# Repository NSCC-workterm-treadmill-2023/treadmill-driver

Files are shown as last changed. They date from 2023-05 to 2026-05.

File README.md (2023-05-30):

# Treadmill Driver

This code is designed to replace the front panel of the Vision Fitness
[T9800 treadmill](https://www.toughtrain.com/vision-fitness/vision-fitness-treadmills/vision-t9800hrt-platform-treadmill) (now discontinued),
interfacing directly with the motor controller board in the bottom.

## Usage

See the [API doc](docs/API.md) for recommended usage. You can still use the old way though:

Hold the Nucleo's user button down to raise the treadmill, increasing the elevation. Hold the button down a second time to lower it.
Hold it a third time to raise it again, and so on. The current elevation will be displayed on the LCD screen.

## Hardware

* STM32 Nucleo [G071RB](https://www.st.com/en/evaluation-tools/nucleo-g071rb.html), because it runs at 3.3V.
* A [I2C 1602 LCD](http://www.handsontec.com/dataspecs/module/I2C_1602_LCD.pdf) display, for displaying the current elevation.
* An [Arduino ethernet shield V1](https://docs.arduino.cc/retired/shields/arduino-ethernet-shield-without-poe-module).

## Setup

In Arduino IDE,

1. Add https://github.com/stm32duino/BoardManagerFiles/raw/main/package_stmicroelectronics_index.json to *Additional boards manager URLs* in the preferences.
1. In Tools > Board > Boards Manager, search for Nucleo. Add *STM32 MCU based boards*.
1. In Tools > Board > STM32 MCU based boards, choose *Nucleo-64*. Avoid *Generic STM32G0 series*.
1. In Tools > Board part number, choose *Nucleo G071RB*.
1. In the library manager, install [LiquidCrystal I2C](https://github.com/johnrickman/LiquidCrystal_I2C), [Ethernet](https://www.arduino.cc/reference/en/libraries/ethernet/) and [MQTT](https://github.com/256dpi/arduino-mqtt).

Then hook everything up according to this schematic:

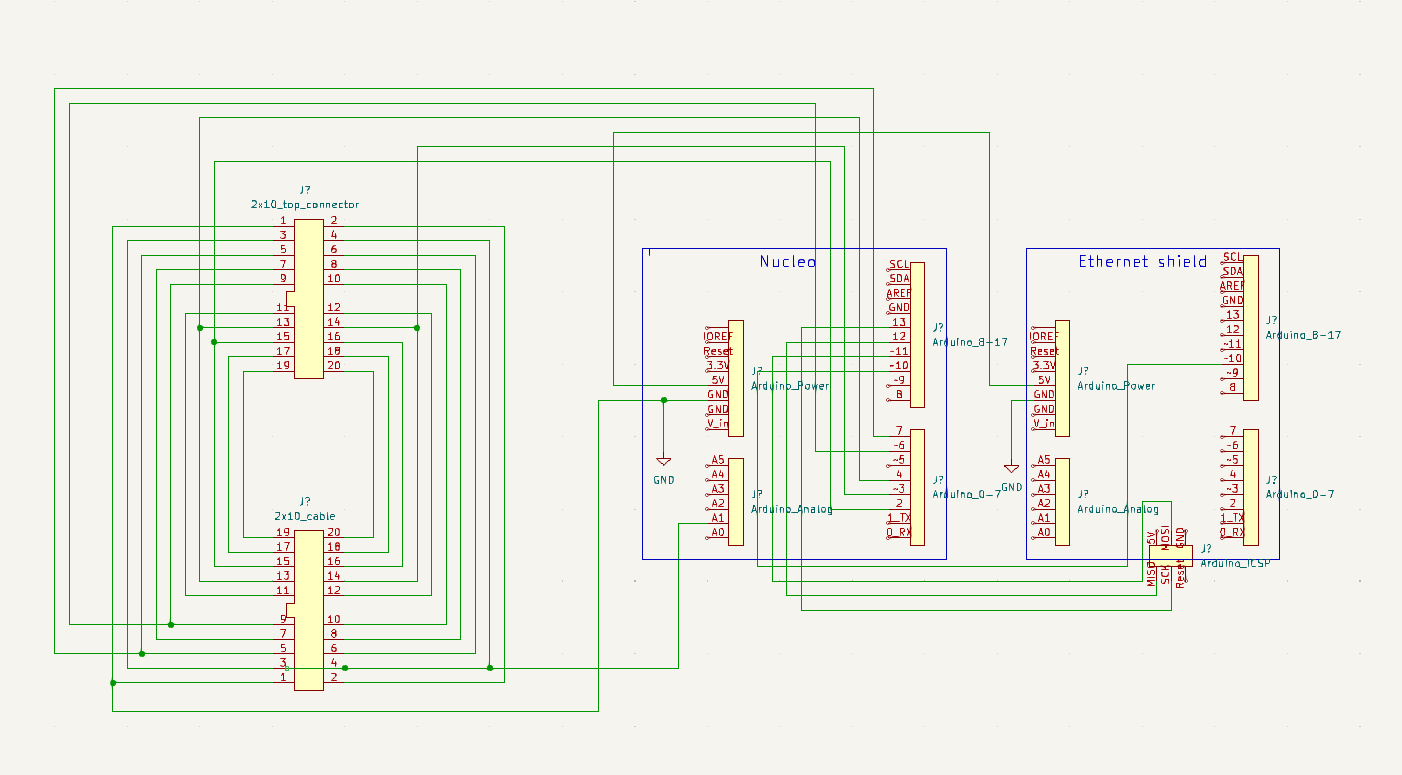
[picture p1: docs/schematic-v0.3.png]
Schematic


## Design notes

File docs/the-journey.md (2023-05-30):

# The journey to a fancy smart treadmill

The goal of this project was to replace the front panel of the
[T9800 treadmill](https://www.toughtrain.com/vision-fitness/vision-fitness-treadmills/vision-t9800hrt-platform-treadmill) with a touchscreen.
I had some web developers to handle the UI, so my job was to interface with the treadmill's motor controller and make it available over a
network.

There was no technical documentation for the treadmill. The JTAG headers didn't work, nor did the
[CSAFE](https://en.wikipedia.org/wiki/Communications_Specification_for_Fitness_Equipment) port, so I was left with reverse-engineering the
signals between the top panel and the motor controller. I did find a engineering manual for repairmen though, which revealed the secret
engineering mode. That gave me direct control of the motors, which made deciphering the signals easier.

## Initial discovery

The first step was to disconnect the cable running from the front panel to the motor controller, and patch it through a breadboard. I used
the [Analog Discovery Studio](https://digilent.com/reference/test-and-measurement/analog-discovery-studio/start), so that I could take
advantage of its logic analyzer. But the first step was to grab the multimeter and find the power and ground lines. I found three 12V lines,
three 5V lines and four ground lines, leaving me with ten communication lines.

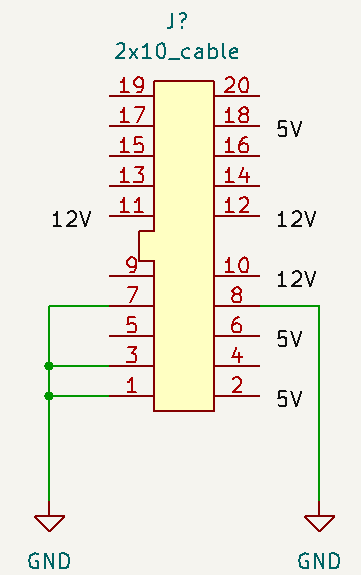
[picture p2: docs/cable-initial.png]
Power and ground wiring


Next, I wired in the DIO pins of the Analog Discovery Studio and took some readings with the logic analyzer. Running through the motions,
I came to believe that elevation was the simplest part, so I started with that. I entered engineering mode, drilled down to the hardware
test, then changed the elevation. Here is what I read:

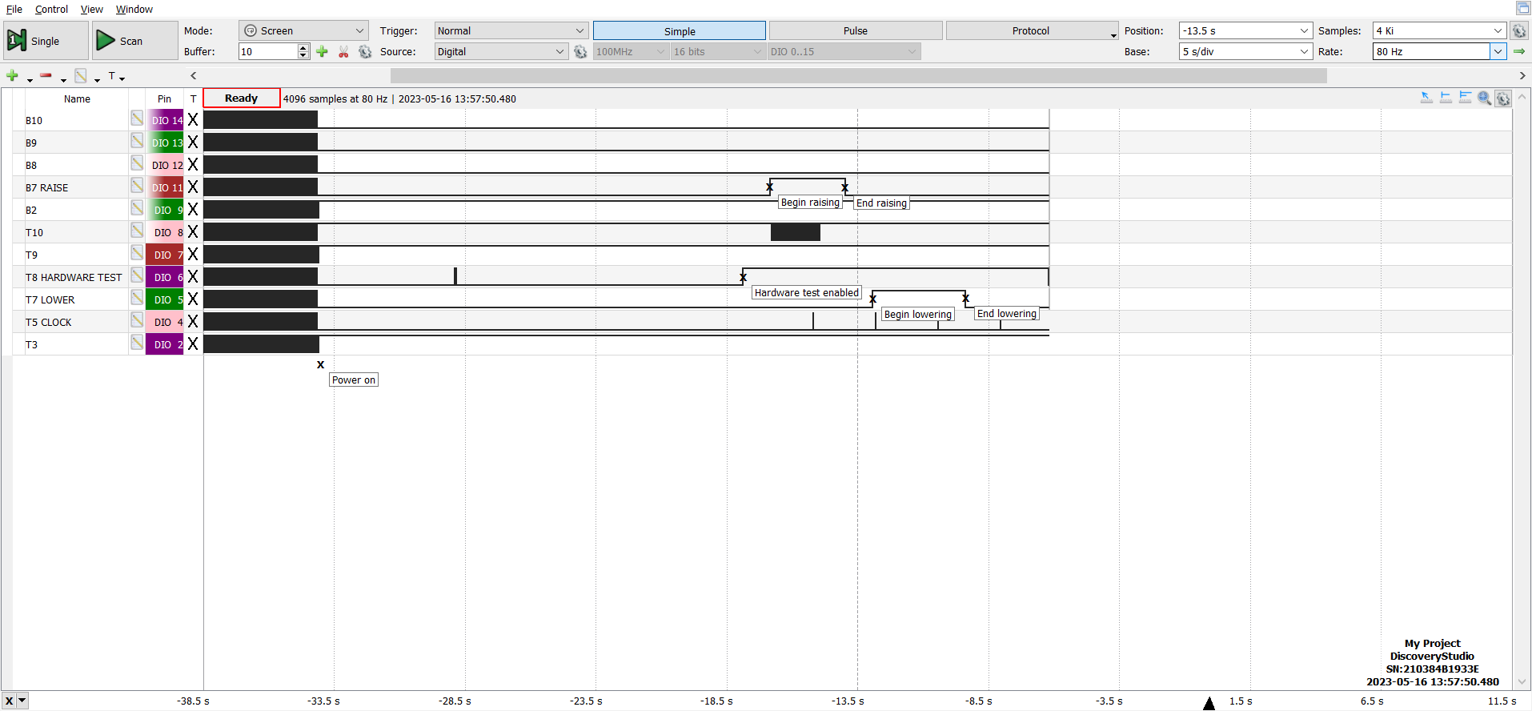
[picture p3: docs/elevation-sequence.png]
Elevation reading


## Deciphering elevation

Clearly, pins 13 (T7) and 14 (B7) control the elevation motor. The hardware test pulls pin 15 (T8) high, and there's a clock running on pin
9 (T5). The other pins going high were a mystery. That was enough to get started. I branched the motor controller cable to a second location
on the breadboard, and added some dip switches to each location. Then I hooked a Raspberry Pi into the new location, because that would make
it easy to provide a REST API for the web devs. With the switches in place, I could switch between the Pi and the front panel without moving
wires around.

Experimentation and trial & error got me some results: Hold pin 15 high, then use pins 13 and 14 to change the elevation (see the [protocol doc](protocol.md)). Everything else turned out to be unnecessary.

Elevation readings proved a bit trickier though. Upon closer inspection with an oscilloscope, I discovered that pin 4 is an analog signal
representing the elevation. The Raspberry Pi doesn't have an ADC, so I switched to an Arduino. The problem with the Arduino is that it
generates 5V signals, while the front panel sends 3.3V signals. I grabbed some resistors and set up some voltage dividers to fix that. But
that presented a new problem: while the Arduino was now sending 3.3V signals in isolation, they dropped to 2V signals when connected to the
motor controller, which were interpreted as digital 0. Rather than finding yet another fix, I switched to an STM32 Nucleo board, which
generates 3.3V signals. That solved the problem and made my circuitry simpler.

With that out of the way, experimentation could continue. I was initially unable to read the elevation, but I eventually discovered that you
need to hold pin 5 high to make the sensor work. And that was all I needed to reach my first milestone: a working elevation demo. See git
tag: v0.1-elevation for the result.

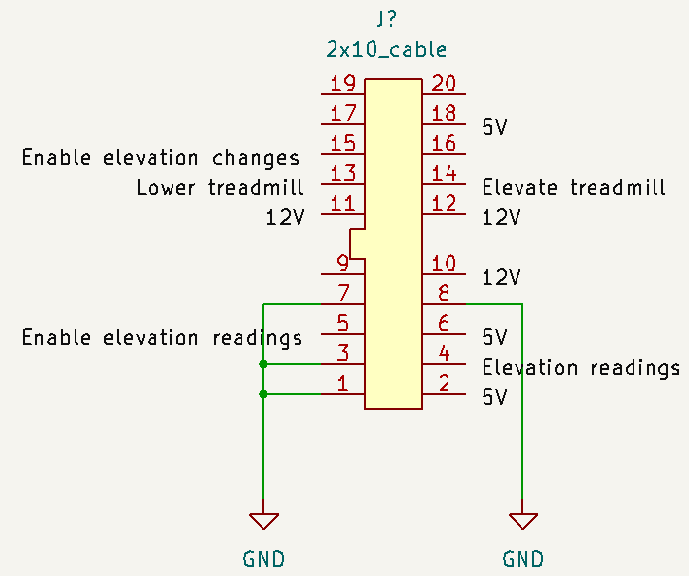
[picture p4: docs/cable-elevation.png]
Elevation wiring


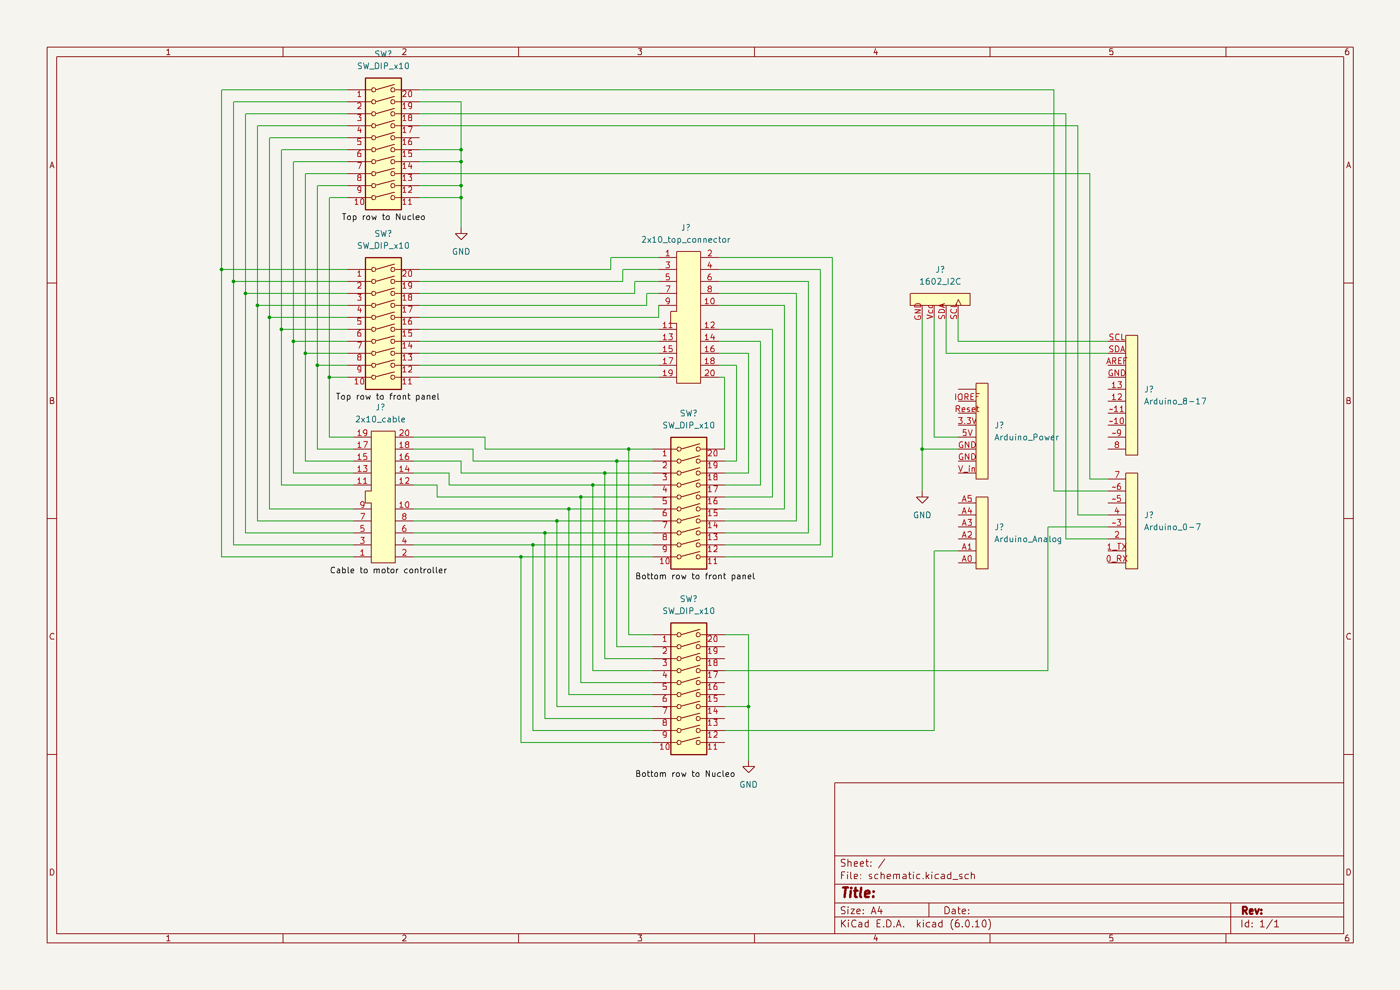
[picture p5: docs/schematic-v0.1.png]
Elevation demo schematic


## Putting it on the network

The next job was to put the treadmill on the network, so that the web devs could start communicating with it. So I added an
[ethernet shield](https://docs.arduino.cc/retired/shields/arduino-ethernet-shield-without-poe-module) to the mix. That turned out to be
a bit trickier than expected. Unlike most shields, that one doesn't respond to the standard SPI pins, except for chip select. Instead,
it uses the SPI pins of the ICSP headers. That made wiring tough, but it was straightforward enough once I saw the problem.

From there, it was relatively smooth sailing. I installed [mosquitto](https://mosquitto.org/) on the touchscreen, and added some code
to communicate with it. See git tag: v0.2-mqtt for the result.

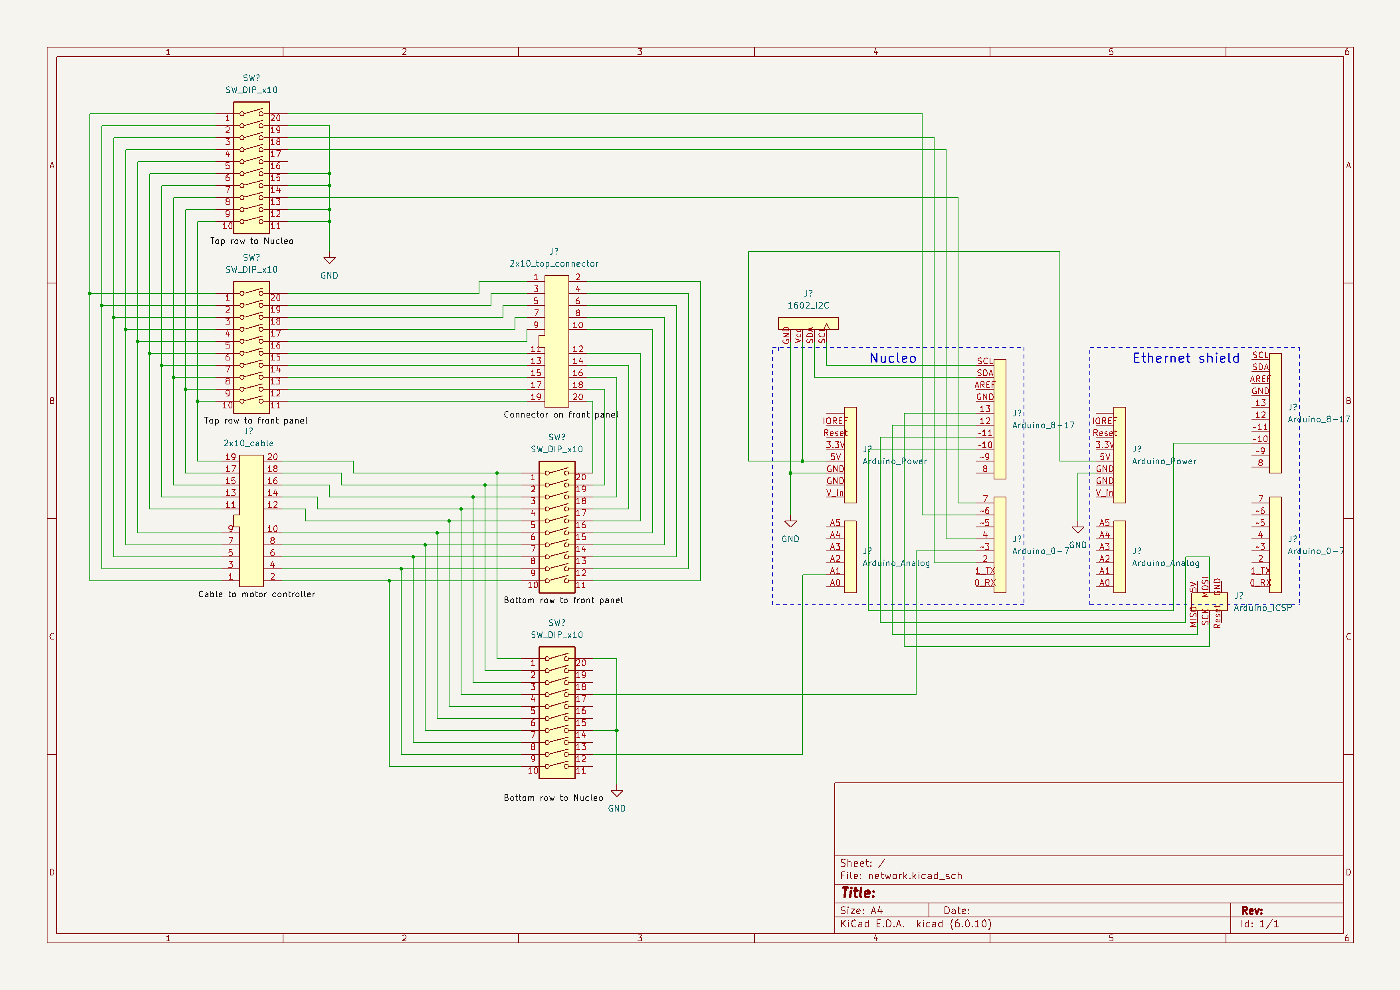
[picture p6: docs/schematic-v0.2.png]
Network schematic


## Moving the tread

Then it was time to do the most important part: control the speed, so that the treadmill could actually be used. This proved to be quite
problematic, because I was stymied by faulty connections. Switching back to the front panel, I couldn't get the motor to move. However,
it worked if I unplugged all my wires and plugged the cable directly into the front panel, as it shipped from the factory. I plugged my
wires back in and tested continuity on every part of it. Everything looked peachy, so I tried to run the treadmill, but the motor still
wouldn't turn.

Assuming that some of my wires were low quality, I cut my own wires off some spools of wire. 40 snips and 80 ends stripped later, I had
everything hooked up with presumably good connections. And yet, that motor still refused to move. In the end, I made a ribbon cable to
connect the built-in cable to the front panel, and added a third connector in the middle of the ribbon. The third connector gave me a
spot to hook up the Nucleo, the logic analyzer, the oscilloscope and the multimeter. And **finally**, a whole week later, it worked!

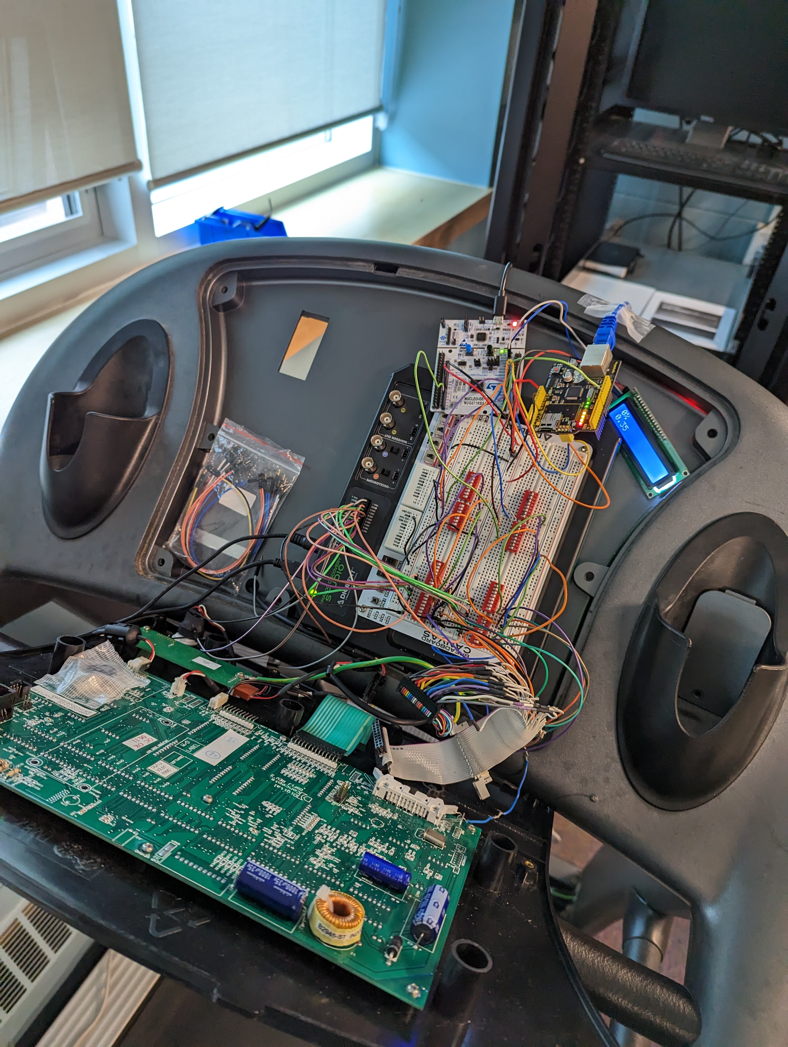
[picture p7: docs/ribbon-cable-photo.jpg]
Ribbon cable setup


Now I could get some readings, and I was off to the races. This is what I saw:

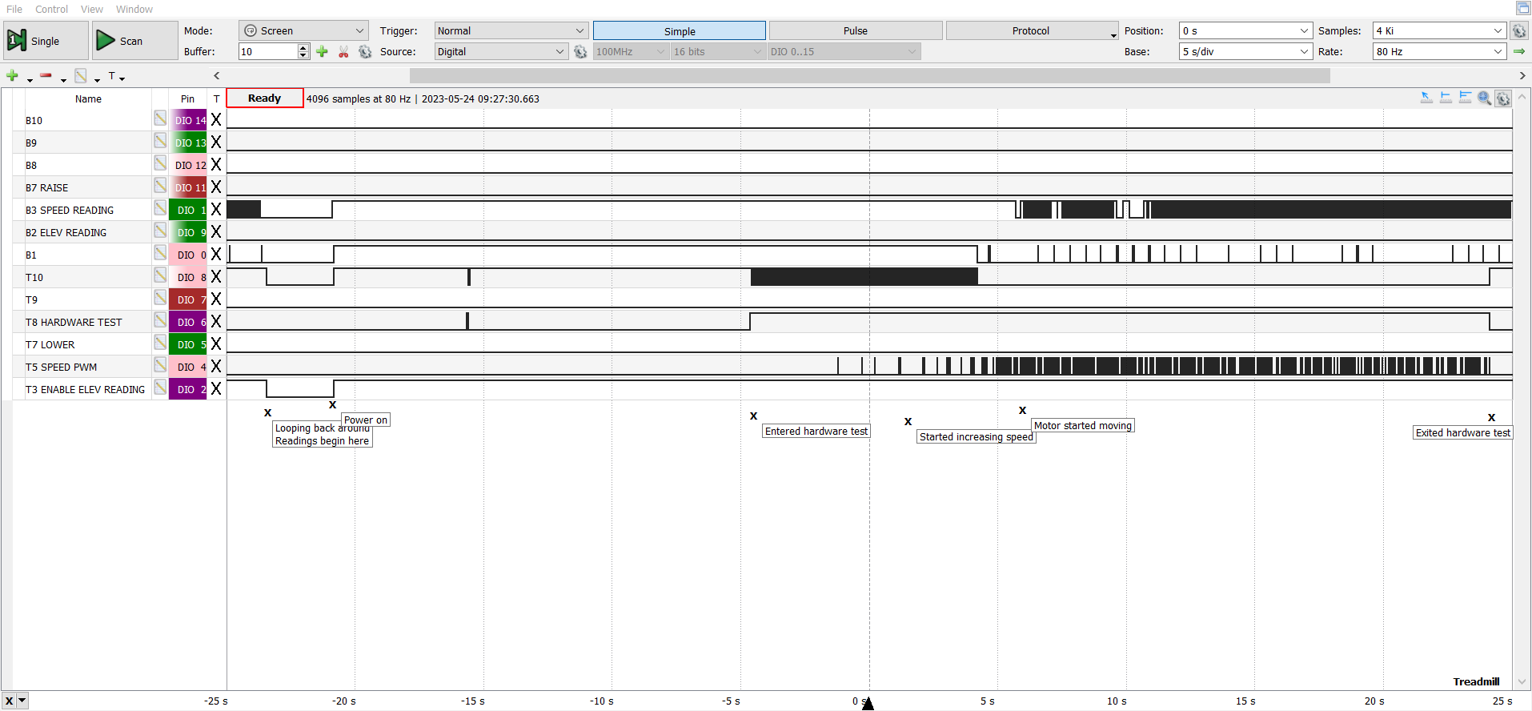
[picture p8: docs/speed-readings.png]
Speed reading


Looking closer with the oscilloscope, I could see that the speed control was a simple PWM signal. The speed sensor was a bit trickier.
It looks like a PWM signal, but the duty cycle was always 50%. Instead, the period decreases as the speed increases. That turned out to
be due to the nature of the sensor itself &mdash; a cog wheel with a magnetic sensor to sense cogs and gaps.

All that was left was calibration. I had initially tried measuring the period with the oscilloscope, and then comparing it to the speed
reported by the front panel, but that gave wildly inaccurate results. After a few variations on that strategy, I gave up and just timed
the tread with a stopwatch. Once I had some data points [desmos](https://www.desmos.com/calculator) made finding the curve of best fit
easy.

Final schematic

## Final stretch

And that was just about it. I put the speed sensor and speed control on MQTT, and the web devs made the treadmill dance from their fancy
UI on the touchscreen. Mission accomplished! Well, sort of. The project was over, and I hadn't even got started on the heart rate sensor.
Still, I'm happy with what I achieved.

A big thanks to my teacher Brian Shewan for helping me through the hard parts!

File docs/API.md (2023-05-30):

# Treadmill API

The treadmill communicates over MQTT. The treadmill has a unique identifier: **T9800-1**. All MQTT topics for the treadmill are prefixed with
/T9800-1. That allows us to control multiple treadmills from a single MQTT broker later, if we desire.

## Elevation

Subscribe to /{id}/readings/elevation to get the current elevation. This broadcasts an integer from 0 to 15, where 0 is flat and 15 is the
maximum incline.

Publish to /{id}/control/elevation to change the current elevation. This accepts an integer from 0 to 15, where 0 is flat and 15 is the
maximum incline. Numbers less than 0 will be treated as 0. Numbers greater than 15 will be treated as 15.

## Speed

Subscribe to /{id}/readings/speed to get the current speed as a float in km/h.

Publish to /{id}/control/speed to change the current speed.

Values below 0 will be treated as 0. Values above 24 will be treated as 24.

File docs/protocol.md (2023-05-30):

# Treadmill Protocol

This interfaces directly with the treadmill connector, which would ordinarily connect the front panel up top to the motor controller
in the bottom. The treadmill connector has a notch on top. Pin 1 is top left, pin 2 is under pin 1, pin 3 is to the right of pin 1, pin 4 is
under pin 2, and so on.

## Elevation

### Reading elevation

The elevation sensor is a potentiometer. Put power on pin 5 and ground on pin 3, then read the analog signal on pin 4. Note that the pot's
ground is not connected to any other ground - you should do that yourself. For a 3.3V input, the minimum value is 0.8V, representing a flat
treadmill. The maximum value is 3.12V, representing the steepest incline possible.

### Changing elevation

Hold pin 15 high to warm up the motors and enable elevation changes. Then hold pin 14 high to increase the elevation, **or** hold pin 13 high
to decrease the elevation. The motor controller has safeguards in place, so you can't go past the minimum and maximum values.

## Speed

### Reading speed

The speed sensor senses a rotating cog attached to the motor. A magnetic sensor is placed in line with the cogs. When a cog is in front of a sensor,
the line goes high. When there's a gap in front of the sensor, the line goes low (or maybe it's vice versa). You can deduce the speed by measuring
the time between changes in the signal. Read the signal on pin 6.

### Changing speed

This one's simple: just put a PWM signal on pin 9. I think you need to hold pin 15 high for this to work, but I haven't tried without it.

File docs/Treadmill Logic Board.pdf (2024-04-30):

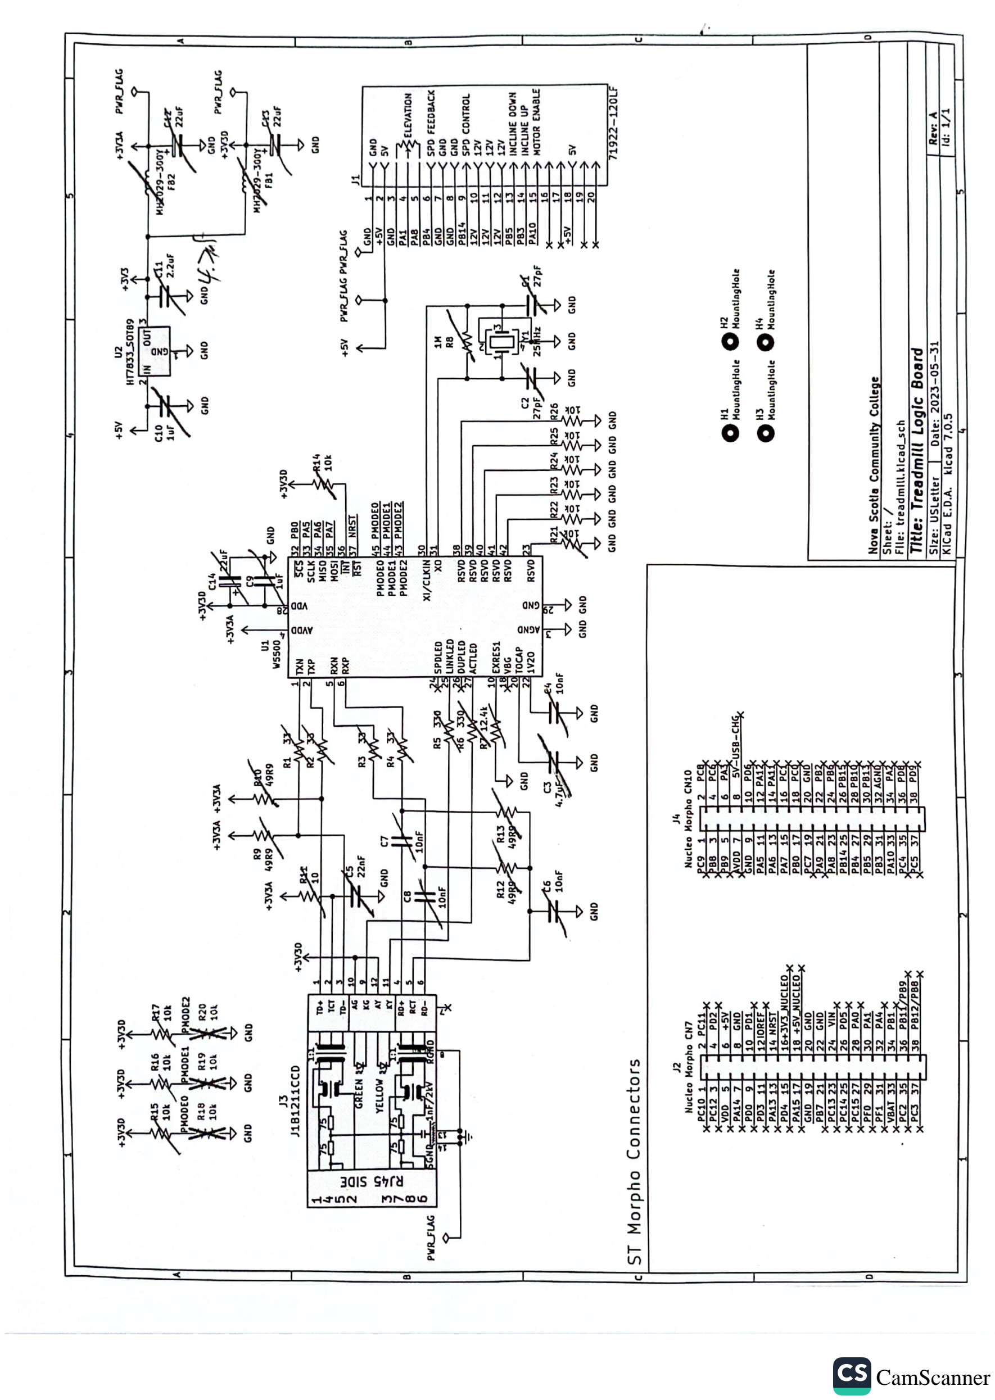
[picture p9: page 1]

CamScanner (https://v3.camscanner.com/user/download)

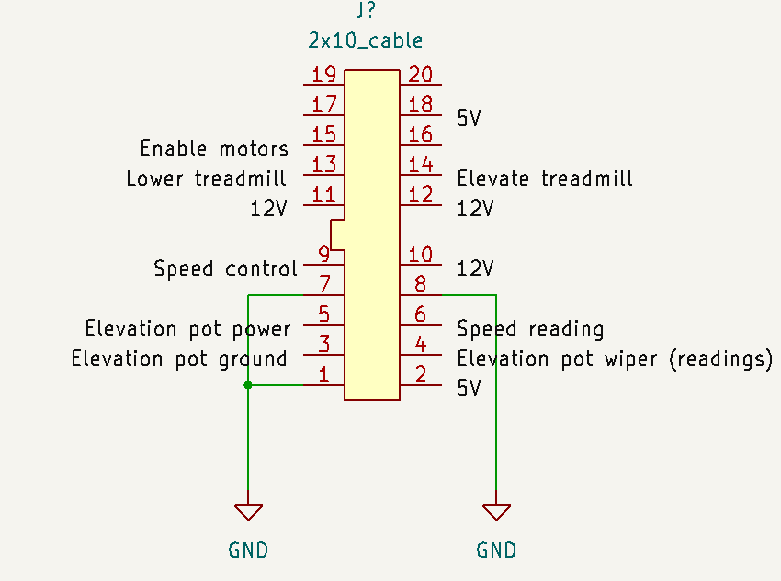
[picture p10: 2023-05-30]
docs/cable-final.png

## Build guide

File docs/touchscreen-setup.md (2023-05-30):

# Touchscreen setup

1. Configure the ethernet port to have static IP 192.168.5.1
1. Install [Mosquitto](https://mosquitto.org/) MQTT broker to `C:\Program Files\mosquitto` (the default location)
1. Give it the following configuration in mosquitto.conf:

```
listener 1883 0.0.0.0
allow_anonymous true
```

The Nucleo uses 192.168.5.2.

## Security concerns

* Mosquitto is currently wide open to the world. It should be locked down to localhost (for the web backend) and 192.168.5.1 (for the Nucleo)
* Authentication and TLS should be configured for MQTT, if the Arduino lib supports that.
* The network is currently 192.168.5.0/24. If we made it /30, then an attacker couldn't get an IP, because the only available ones would be in use.

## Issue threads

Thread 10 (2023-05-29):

Speed readings should have a timeout

W0481966, 2023-05-29:
If the speed sensor doesn't change after a second or two, you should report a speed of 0km/h.

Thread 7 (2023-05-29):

LCD and user button should be removed from final product

W0481966, 2023-05-29:
They're good for debugging and demoing, but they'll be out of sight and out of reach in the end.

JayPankajPatel, 2023-05-29:
Hey I would like to work on this issue, I was wondering if I could get more details on the where in the code these interfaces are used

W0481966, 2023-05-29:
Look for `BUTTON` for the button. The LCD is used in `displayIncline()` and `displaySpeedSensorTime()`, and of course `setup()` and the variable definitions up top.

JayPankajPatel, 2023-05-29:
Do you think making a conditional compilation statement might be better just in case it might be needed again for debugging or should I just go ahead and remove it.

JayPankajPatel, 2023-05-29:
Also could you assign the issue to me

Closed 2023-06-01.

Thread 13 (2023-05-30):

Add diagnostics

W0481966, 2023-05-30:
The front panel has a feature where it'll error out if the speed sensor doesn't report the speed that's being sent on the PWM signal. Same deal with elevation. We should do the same.

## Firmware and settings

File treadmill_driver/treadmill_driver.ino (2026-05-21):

#include <Ethernet.h>
#include <MQTTClient.h>
#include <stdint.h>

// MQTT setup
#define MQTT_CLIENT_NAME "treadmill_controller"
#define MQTT_PORT 1883
#define MQTT_INTERVAL 100
#define TREADMILL_ID "T9800-1"

// MQTT topics
#define TOPIC_CONTROL_ELEVATION "/control/elevation"
#define TOPIC_CONTROL_SPEED "/control/speed"
#define TOPIC_READINGS_ELEVATION "/readings/elevation"
#define TOPIC_READINGS_SPEED "/readings/speed"
#define TOPIC_EMERGENCY "/emergency"

// Pin definitions
#define ENABLE_ELEV_CHANGE 2
#define RAISE 3
#define LOWER 4
#define ENABLE_ELEV_READ 7
#define ELEV_READ A1
#define SPEED_CHANGE 6
#define SPEED_READ 5
#define REED_SWITCH_PIN 9

const uint16_t INCLINE_ADC_ZERO = 185;
volatile bool inclineRequested = false;
uint16_t desiredIncline = 210;

#define SPEED_SENSOR_BUFFER_SIZE 10
#define INCLINE_TOLERANCE_ADC 10
#define INCLINE_ADC_MIN 210
#define INCLINE_ADC_MAX 800
#define SPEED_MIN 0
#define SPEED_MAX 7
#define INCLINE_STALL_TIMEOUT_MS 500
#define SPEED_STALL_TIMEOUT_MS 500
#define INCLINE_STALL_MOVEMENT_THRESHOLD 5
volatile uint32_t speedSensorChangeTimes[SPEED_SENSOR_BUFFER_SIZE] = {0};
volatile uint8_t speedSensorIndex = 0;

// Safety state enum
enum SafetyStatus { SAFE, UNSAFE };

EthernetClient ethClient;
MQTTClient mqtt = MQTTClient(256);
uint8_t mac[] = {0xDE, 0xAD, 0xBE, 0xEF, 0xFE, 0xED};
IPAddress localIP(192, 168, 5, 2);
IPAddress brokerIP(192, 168, 5, 1);
uint32_t lastMqttSendTime = 0;

volatile SafetyStatus safetyState = SAFE;
volatile bool safetyStateChanged = false;

uint32_t stallCheckTime = 0;
uint16_t stallCheckADC = 0;



void setup() {
  Serial.begin(115200);
  Ethernet.begin(mac, localIP);

  pinMode(ENABLE_ELEV_CHANGE, OUTPUT);
  pinMode(ENABLE_ELEV_READ, OUTPUT);
  pinMode(RAISE, OUTPUT); 
  pinMode(LOWER, OUTPUT);
  pinMode(SPEED_CHANGE, OUTPUT);
  pinMode(SPEED_READ, INPUT);
  pinMode(REED_SWITCH_PIN, INPUT_PULLUP);

  attachInterrupt(digitalPinToInterrupt(SPEED_READ), speedSensorInterruptHandler, CHANGE);
  attachInterrupt(digitalPinToInterrupt(REED_SWITCH_PIN), reedSwitchInterruptHandler, CHANGE);

  connectToMQTT(brokerIP, ethClient);

  digitalWrite(ENABLE_ELEV_READ, HIGH);
  digitalWrite(ENABLE_ELEV_CHANGE, HIGH);

  publish(TOPIC_CONTROL_ELEVATION, (long)INCLINE_ADC_ZERO);  //Set elevation to 0 on startup

  Serial.println("System Initialized");

  safetyState = (digitalRead(REED_SWITCH_PIN) == HIGH) ? SAFE : UNSAFE;
}

void loop() {
  if (safetyStateChanged) {
    safetyStateChanged = false;
    if (safetyState == SAFE) {
      publish(TOPIC_EMERGENCY, "false");
    } else {
      publish(TOPIC_EMERGENCY, "true");
    }
  }

  if (!mqtt.connected()) connectToMQTT(brokerIP, ethClient);

  mqtt.loop();
  changeIncline(desiredIncline);

  if (millis() - lastMqttSendTime >= MQTT_INTERVAL) {
    lastMqttSendTime = millis();

    publish(TOPIC_READINGS_ELEVATION, (long)analogRead(ELEV_READ));

    // Disable interupts to prevent race condition while reading speed values
    noInterrupts();
    uint8_t idx = speedSensorIndex;
    uint32_t newest = speedSensorChangeTimes[idx];
    uint32_t oldest = speedSensorChangeTimes[(idx + 1) % SPEED_SENSOR_BUFFER_SIZE];
    uint32_t now = micros();
    interrupts();
    
    // prevent erroneous startup values where the buffer is 0s
    if (oldest == 0) {
      publish(TOPIC_READINGS_SPEED, 0.0f);
    } else if (now - newest > (uint32_t)SPEED_STALL_TIMEOUT_MS * 1000UL) {
      // No pulse received recently - belt has stopped
      publish(TOPIC_READINGS_SPEED, 0.0f);
    } else {
      uint32_t averagePeriod = (newest - oldest) / (SPEED_SENSOR_BUFFER_SIZE - 1);
      publish(TOPIC_READINGS_SPEED, periodToSpeed(averagePeriod));
    }
  }
}

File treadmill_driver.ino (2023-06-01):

#include <Ethernet.h>
#include <MQTTClient.h>

#define MQTT_CLIENT_NAME "treadmill_controller"
#define MQTT_INTERVAL 100
// A unique ID to use in our MQTT topics, in case we want to connect multiple
// treamills to the same broker.
#define TREADMILL_ID "T9800-1"

#define ENABLE_ELEV_CHANGE 2
#define RAISE 3
#define LOWER 4
#define ENABLE_ELEV_READ 7
#define ELEV_READ A1
#define SPEED_CHANGE 6
#define SPEED_READ 5

enum Direction {UP, DOWN};

int desiredIncline = 0;
bool inclineChangeRequested = false;
int direction = UP;

#define SPEED_SENSOR_BUFFER_SIZE 10
long speedSensorChangeTimes[] = {0, 0, 0, 0 ,0, 0, 0, 0, 0, 0};
unsigned int speedSensorIndex = 0;

EthernetClient ethClient;
MQTTClient mqtt = MQTTClient(256); // Param is max packet size
byte mac[] = {0xDE, 0xAD, 0xBE, 0xEF, 0xFE, 0xED};
IPAddress localIP(192, 168, 5, 2);
IPAddress brokerIP(192, 168, 5, 1);
uint32_t lastMqttSendTime = 0;

void subscribe(const char *topicSuffix) {
  String topic = String("/");
  topic.concat(TREADMILL_ID);
  topic.concat(topicSuffix);

  mqtt.subscribe(topic);
}

void publish(const char *topicSuffix, const char *message) {
  String topic = String("/");
  topic.concat(TREADMILL_ID);
  topic.concat(topicSuffix);

  mqtt.publish(topic, message);
}

void publish(const char *topicSuffix, long message) {
  publish(topicSuffix, String(message).c_str());
}

void publish(const char *topicSuffix, float message) {
  publish(topicSuffix, String(message).c_str());
}

long inclineAsPercentage(int ADCReading) {
  // The user manual says that incline is between 0% and 15%
  return map(ADCReading, 156, 796, 0, 15);
}

/* Takes speed in km/h as input, and outputs a value for use with analogWrite()
 *
 * The numbers used in these calculations were decided on by measuring the
 * belt's rotation time at various speeds with a stopwatch, and using desmos
 * to find the line of best fit.
 *
 * https://help.desmos.com/hc/en-us/articles/4406972958733-Regressions */
int speedToPWMSignal(float speed) {
  return 7.680178 * speed + 3.19791;
}

/* Takes a period in microseconds as input, and outputs the speed it represents
 * in km/h. Technically, it's only half a period - the distance of a cog or gap
 * in the sensor.
 *
 * As above, we're using desmos to find the curve of best fit - this time it's
 * a reciprocal function, since there's a linear relationship between frequency
 * and speed, but we're measuring period.
 *
 * https://help.desmos.com/hc/en-us/articles/4406972958733-Regressions */
float periodToSpeed(long period) {
  return 13094.3 / ((float) period + 169.358) - 0.204098;
}

/* The speed sensor is built on a rotating cog wheel with a magnetic sensor.
 * When a cog is in front of the sensor, it goes high, and when there's a
 * gap, it goes low (or maybe it's vice versa). By measuring the frequency
 * or period of the changes, we can deduce the speed.
 *
 * The sensor triggers frequently - multiple times per loop iteration. So we
 * add a buffer, and store the last SPEED_SENSOR_BUFFER_SIZE readings in it.
 * Rather than keeping the buffer array sorted, we simply store the index of
 * the most recent reading. */
void speedSensorInterruptHandler() {
  speedSensorIndex = (speedSensorIndex + 1) % SPEED_SENSOR_BUFFER_SIZE;
  speedSensorChangeTimes[speedSensorIndex] = micros();
}

void setSpeed(float speed) {
  analogWrite(SPEED_CHANGE, speedToPWMSignal(speed));
}

void receive(String &topic, String &payload) {
  if (topic.endsWith("/control/elevation")) {
    long elevation = payload.toInt();
    if (elevation < 0) elevation = 0;
    else if (elevation > 15) elevation = 15;

    desiredIncline = elevation;
    inclineChangeRequested = true;
  } else if (topic.endsWith("/control/speed")) {
    float speed = payload.toFloat();
    if (speed > 24) speed = 24;
    else if (speed < 0) speed = 0;

    setSpeed(speed);
  }
}

void connectToMQTT() {
  mqtt.begin(brokerIP, 1883, ethClient);

  while (!mqtt.connect(MQTT_CLIENT_NAME)) {
    delay(100);
  }

  if (!mqtt.connected()) {
    return;
  }

  mqtt.onMessage(receive);
  subscribe("/control/elevation");
  subscribe("/control/speed");
}

void setup() {
  Serial.begin(9600);

  Ethernet.begin(mac, localIP);
  connectToMQTT();

  pinMode(ENABLE_ELEV_CHANGE, OUTPUT);
  pinMode(ENABLE_ELEV_READ,   OUTPUT);

  pinMode(RAISE,  OUTPUT);
  pinMode(LOWER,  OUTPUT);
  pinMode(SPEED_CHANGE, OUTPUT);
  pinMode(SPEED_READ,   INPUT);

  digitalWrite(ENABLE_ELEV_READ, HIGH);
  digitalWrite(ENABLE_ELEV_CHANGE, HIGH);

  attachInterrupt(digitalPinToInterrupt(SPEED_READ), speedSensorInterruptHandler, CHANGE);
}

void changeIncline(long currentIncline) {
  if (!inclineChangeRequested) return;

  if (desiredIncline > currentIncline) {
    digitalWrite(RAISE, HIGH);
  } else if (desiredIncline < currentIncline) {
    digitalWrite(LOWER, HIGH);
  } else {
    digitalWrite(RAISE, LOW);
    digitalWrite(LOWER, LOW);
    inclineChangeRequested = false;
  }
}

void loop() {
  if (!mqtt.connected()) connectToMQTT();

  long currentIncline = inclineAsPercentage(analogRead(ELEV_READ));
  changeIncline(currentIncline);

  if (millis() - lastMqttSendTime >= MQTT_INTERVAL) {
    lastMqttSendTime = millis();

    publish("/readings/elevation", currentIncline);
    publish("/readings/speed", periodToSpeed(
      speedSensorChangeTimes[speedSensorIndex] - speedSensorChangeTimes[(speedSensorIndex - 1) % SPEED_SENSOR_BUFFER_SIZE]
    ));
    mqtt.loop();
  }

}

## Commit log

2023-05-05 Have a debounced button.
2023-05-05 Button alternates between raising and lowering the treadmill when pressed.
2023-05-09 Now using onboard button to control elevation.
2023-05-16 Have schematic of my setup.
    [schematic.kicad_sch]
2023-05-16 Added schematic diagram to readme.
2023-05-16 Finished the journey doc, for now.
    [cable-elevation.kicad_sch, cable-initial.kicad_sch]
2023-05-16 Added documentation.
    [network.kicad_pcb, network.kicad_sch, schematic-v0.1.kicad_sch]
2023-05-16 Added second schematic to journey doc.
2023-05-25 Named elevation reading pin.
2023-05-30 removed button and lcd display logic
2023-05-30 Added documentation for speed.
    [cable-final.kicad_pcb, cable-final.kicad_sch, schematic-final.kicad_pcb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]
2023-05-31 (#12) Removed LCD from schematic and README
    [schematic-final.kicad_sch]
2023-05-31 Added final schematic png
2024-04-30 Platform Treadmill Service manual and Treadmill Logic Board added
2025-05-21 Reed Switch Emergency stop code Added
2025-05-21 Updated interrupt for Reedswitch
2025-05-22 fixed message not sending when reconnected
    [treadmill_driver.ino]
2025-05-22 reversed reed logic to work correctly
    [treadmill_driver.ino]
2026-05-06 Refactor and enhance incline and speed handling with safety improvements (#14)
    * fix: restored deleted variable declaration to fix compile error
    * fix: marked global variables used in ISR as volatile
    * fix: fix speed to average newest and oldest buffer values
    * refactor: used stdint for explicit int sizes
    * feat: change from 10% band to 10 ADC count band for incline changes
    * fix: explicitly set all elevation pins while raising and lowering
    * fix: move early return to start of changeIncline
    * fix: remove unneeded cast
    * fix: move connectToMQTT to after pins are configured
    * docs: remove old comments
    * fix: move mqtt.loop() out of interval, it processes messages not creates them
    *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
    [elevation.ino, mqtt.ino, speed.ino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]
2026-05-15 feat: change MQTT publishing from time-based to change-based (#16)
    Replace the fixed 100ms MQTT publish interval with change-triggered
    publishing. Both elevation and speed readings are now sent only when they
    change by a significant amount:
    - Elevation: 10 ADC units threshold (mirrors INCLINE_STALL_MOVEMENT_THRESHOLD)
    - Speed: 0.1 km/h threshold (one decimal place precision over 0-7 km/h range)
    This reduces unnecessary network traffic while maintaining responsiveness
    to meaningful sensor changes.
    Changes:
    - Remove MQTT_INTERVAL define and lastMqttSendTime variable
    - Add ELEVATION_PUBLISH_THRESHOLD and SPEED_PUBLISH_THRESHOLD defines
    - Add lastPublishedElevation and lastPublishedSpeed stat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
    [treadmill_driver.ino]
2026-05-15 fix: clamp speeds to 0.0f at slowest (#17)
    [speed.ino]
2026-05-19 Revert "feat: change MQTT publishing from time-based to change-based (#16)"
    This reverts commit 2ad28ab3217c4296911ba18795fd4a05cbc4921b.
    [treadmill_driver.ino]
2026-05-21 fix: reduce incline adc thresholds and switch e-stop to true/false messages
    [treadmill_driver.ino]
